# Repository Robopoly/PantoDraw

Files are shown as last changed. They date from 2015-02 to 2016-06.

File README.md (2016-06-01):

# The PantoDraw
The PantoDraw is a device capable of drawing the portrait of people interacting with it. 

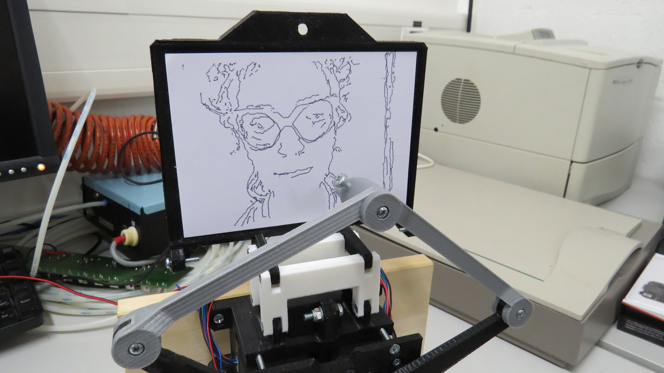
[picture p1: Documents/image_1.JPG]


## Main concept
As visitors always enjoy interacting with robots when visiting Robopoly’s booth at EPFL events, the goal of this project is to give them the opportunity to spend a pleasant time being drawn by a robot-like device. 
By exploiting the capabilities of the [Beagle Bone Black](https://beagleboard.org/black) (BBB), a Texas Instrument single-board powerful computer, and Python programming language, the development team ended up with an original and easy-to-use demonstration of the various skills found at Robopoly.

Operated by a competent user, the device is able to determine the contour of one’s face, compute the optimal path for the pen, and draw the result on a paper the visitor can return with.

An inexpensive webcam and the [OpenCV](http://opencv.org/) image processing library are used for the contours detection. The input image is first converted to grayscale and then goes through a Canny edge detection algorithm, whose parameters can be manually adjusted.
Based on the resulting contours map, a custom algorithm computes the trajectory and minimises the number of branching and raise/drop of the pen.
The resulting image is finally drawn on a paper using three motors: two for the planar movement of the pen and one for the linear movement of the paper support.

## Version 1

The first version of the device was developed for Robopoly’s booth at [Japan Impact](http://www.japan-impact.ch/en/), the annual Japanese convention at EPFL. The process was supervised and control through the Linux terminal using a set of screen, keyboard and mouse connected via a USB hub to the BBB.
The code was rather rudimentary since it was not possible to jump to the previous step, redo the current one or stop the execution. Inverse kinematics equations were computed using a Matlab script, which was also used to optimise the size of the arms.
On the hardware side, servomotors were used, allowing to easily control the pen position with only a few lines of code using the [Adafruit BBB library](https://learn.adafruit.com/setting-up-io-python-library-on-beaglebone-black). Paper was attached to its support by sliding its corners into tiny slits and the complete structure had been 3D printed at Robopoly.

## Version 2

In order to improve the precision - and thus the quality - of the drawing and the usability of the device, both the software and the hardware part have been improved in a second version.
Some servos were replaced by stepper motors, which do not present the internal slack that servos had.
A graphical user interface (GUI) has been designed with Qt Designer and converted to Python using [PyQt4](https://www.riverbankcomputing.com/software/pyqt/intro). It now allows a smooth interaction with the program: it is thus possible to import an image from a file on disk, visualise the different stages of the image, jump to a previous step, change various settings and save them for a future use.
A complete stepper driver module was written with multiple micro-stepping resolutions and a PCB was resigned for the driver integrated chip.

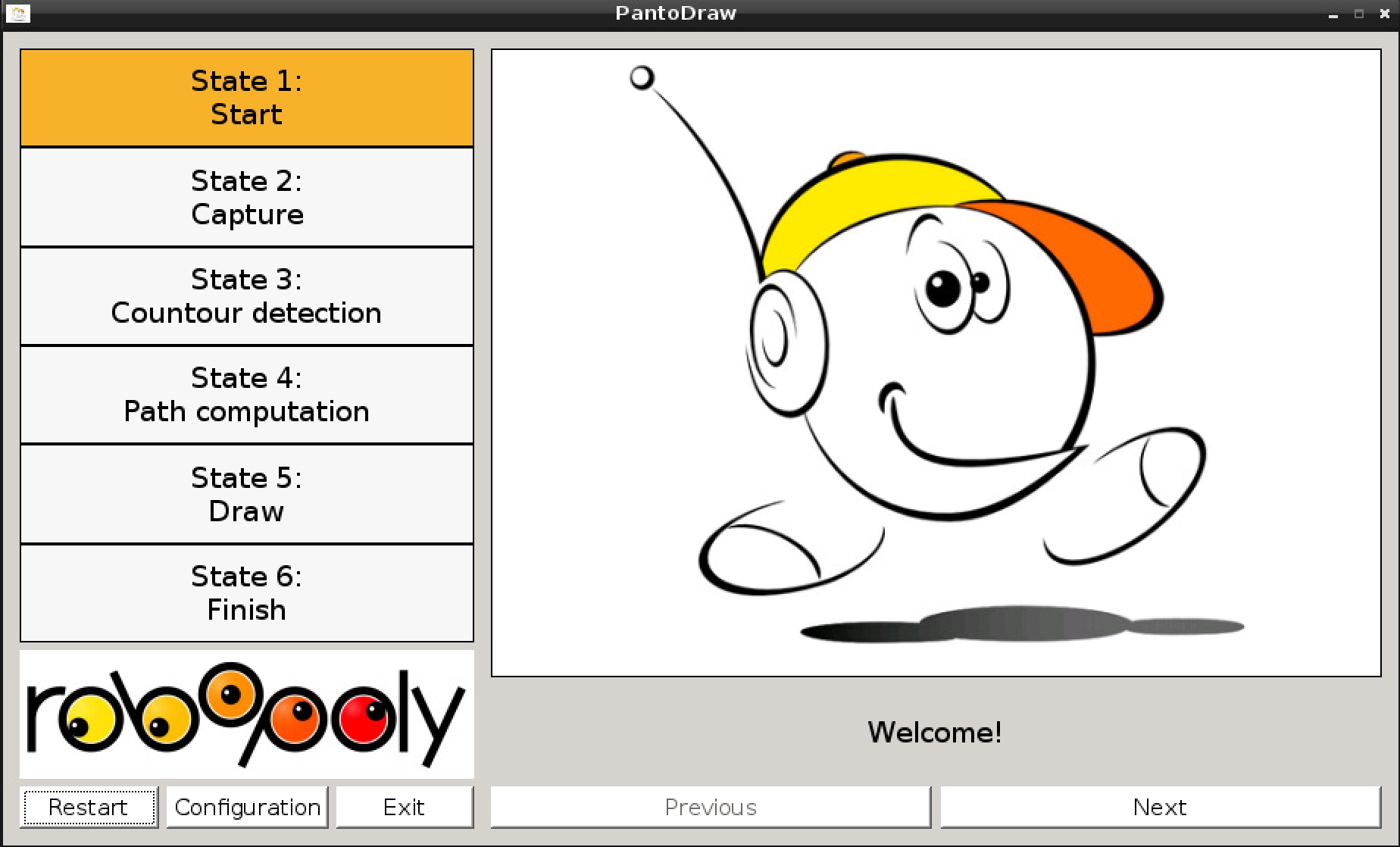
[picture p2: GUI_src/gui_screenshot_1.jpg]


## Hardware

* BeagleBone Black rev. C
* Texas Instrument DRV8823 motor driver
* Bipolar stepper motor 17HM19-2004S (x2)
* Servomotor RS2 MG/BB
* 3D-printed structure
* Folex plotter pen
* A6 paper

## Wiring

The connections to the BBB are:

| Name | Pin |
| ---| --- |
| Driver Data | P9_11  |
| Driver Clock | P9_13  |
| Driver SSTB | P9_15  |
| Driver Chip Select | 5V |
| Servo signal | P9_ 42 |
| VCC | 5V |
| Ground | GND |

The Vbat pin of the driver has to be connected to a DC source which will provide the power for the motors. No exact value is needed since the IC performs a current chop regulation, but there are some conditions: if Vbat is too low, current ramp will be too slow and steps could be missed, but, if V_bat is too high, the driver will dissipate too much heat and its internal thermal shutdown will quickly activate. 20V seems to be working well.

The BBB and the servo have to be powered with a 5V DC source.

The GUI can be accessed with a set of screen/keyboard/mouse or by SSH and VNC with a laptop.

## Use

After boot, the BBB can be access using a simple USB cable connected to a laptop running a VNC client such as Tight VNC Viewer. The address is `192.168.7.2` on port `5900`. The connection requires `X11VNC` to be installed on the board and a simple script to be executed (see folder Documents).

The execution of `main.py` starts the software, including the GUI and the stepper driver module. The user has to make sure both arms are perfectly vertical before launching the drawing.

Future improvement

* Add Endstop micro-switches, allowing to perform an automated calibration of the arms’ position.
* Try a small LCD touchscreen, freeing the operator from the constraint of using a laptop or a screen.
* Improve the pivots could by replacing the 3D printed joints with real bearings.
* Clear the command line script and make it compatible with the modifications introduced by the implementation of the GUI.
* Change the configuration file format from `.py` to `.json` to allow saving of the parameters.

## Credits

Original idea and the first version were developed by Jean-Luc Liardon and Marco Pagnamenta with the help of Pablo Garcia Del Valle, both three members of the Robopoly committee then.

For the second version, the mechanics were designed by Loïs Bosson and Patrick Bobbink, the driver PCB by Yoann Lapijover and the software by Paul-Edouard Sarlin.

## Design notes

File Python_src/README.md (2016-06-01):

# Software

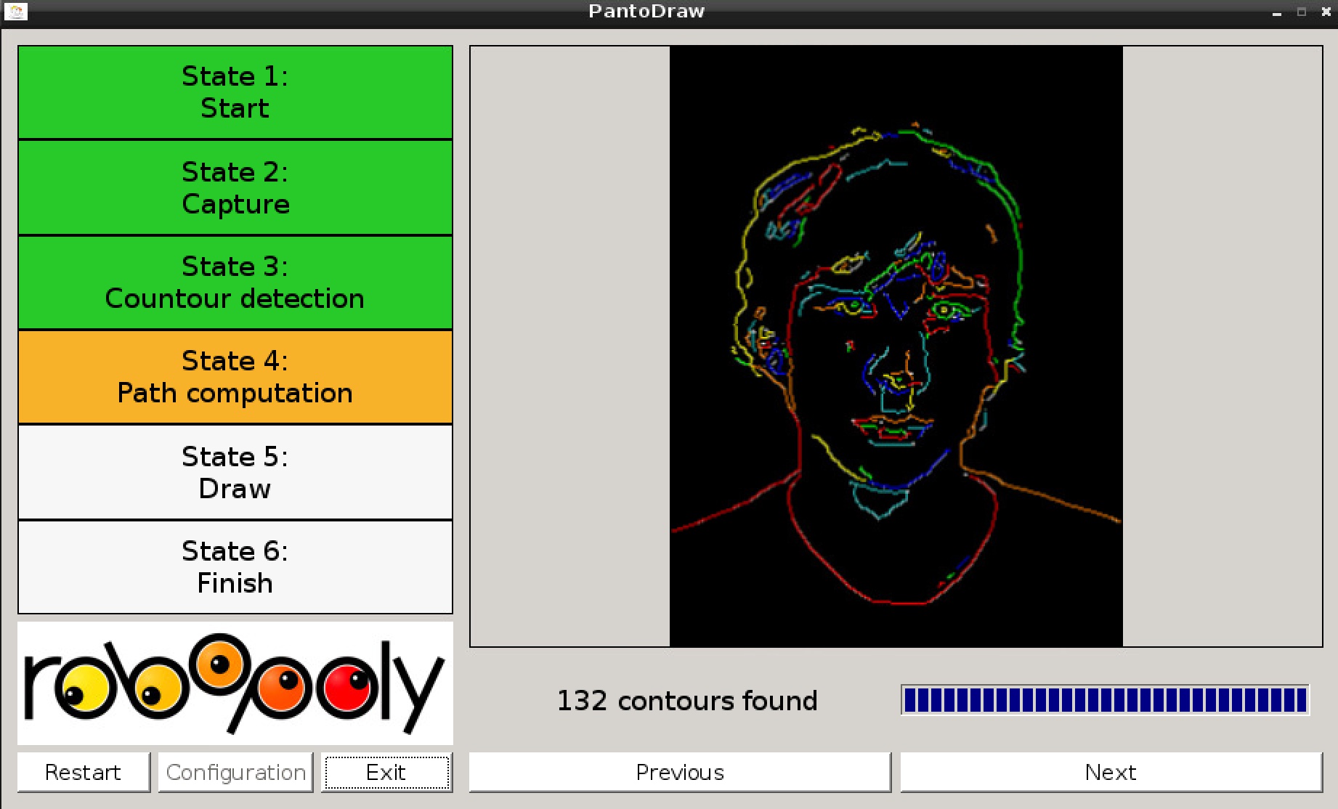
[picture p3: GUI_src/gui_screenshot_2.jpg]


The core application is built around a Finite State Machine (FSM) composed of six states:
* State 1: the starting picture of the software.
* State 2: the acquisition of the image (capture from camera or import from a file on disk).
* State 3: contour detection using the Canny algorithm.
* State 4: path computation and optimisation with display of the different trajectories with various colours.
* State 5: drawing of the result.
* State 6: drawing is finished!

The FSM is directly managed by Qt, running with `main.py`. All the image processing algorithms and OpenCV tools are run in `imageprocessing.py`, which then controls the motor interface (`pantolib_stepper.py` and `stepper.py`).

To ensure that interactions with the GUI are smooth enough even during heavy processing phases, the computations are performed in a separate thread using Python native threading library. The GUI is continuously updated during these phases using `get` functions from the processing module.

Parameters which can be modified by a configuration dialog window in the main application are stored in the `config.py` file and can be easily accessed by the other modules.

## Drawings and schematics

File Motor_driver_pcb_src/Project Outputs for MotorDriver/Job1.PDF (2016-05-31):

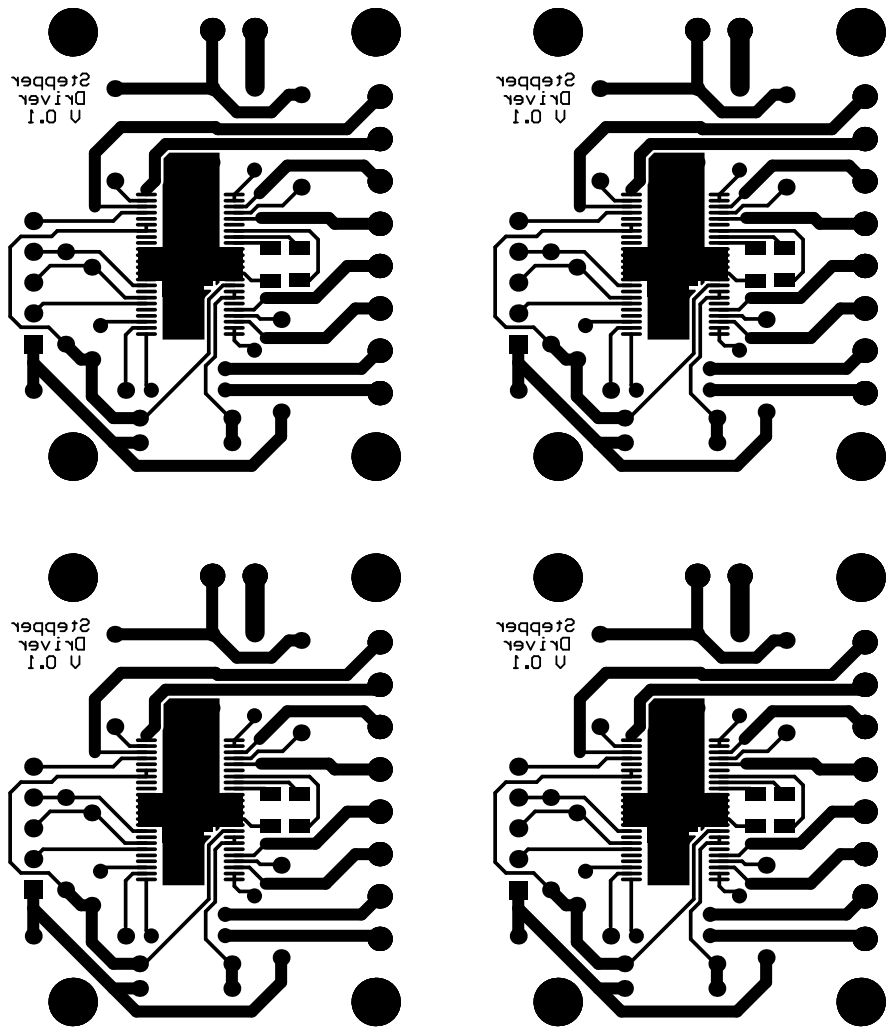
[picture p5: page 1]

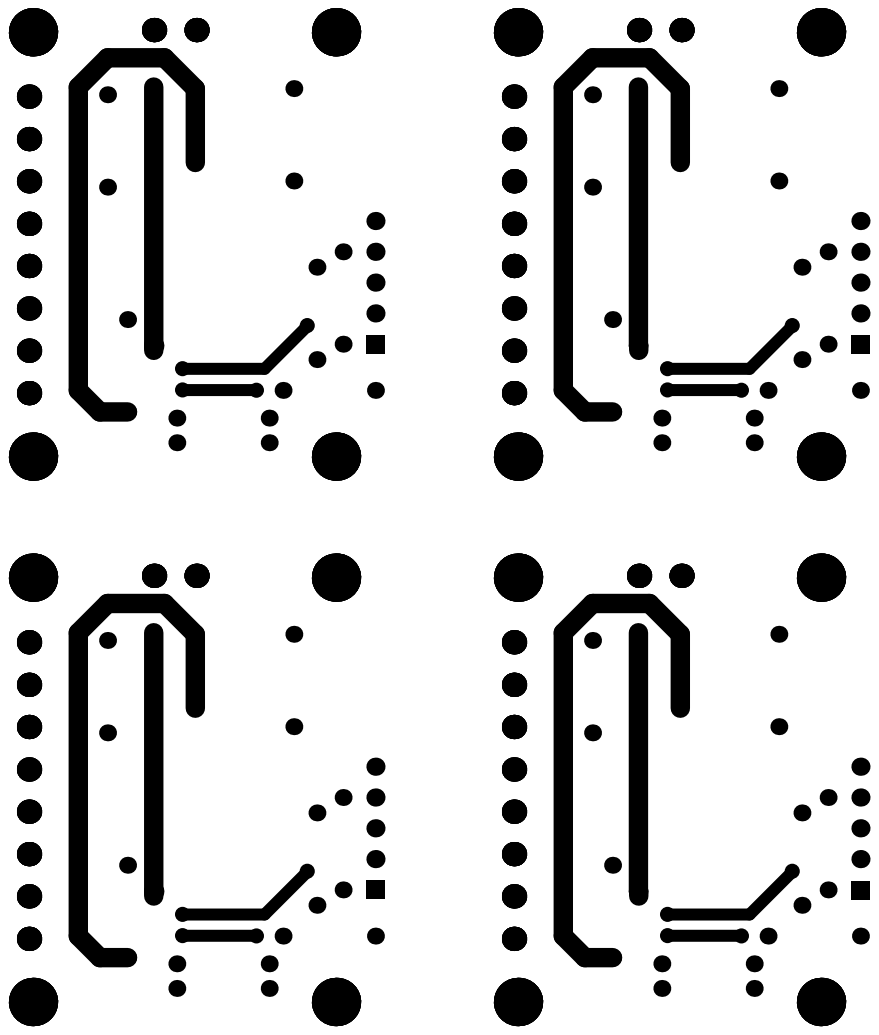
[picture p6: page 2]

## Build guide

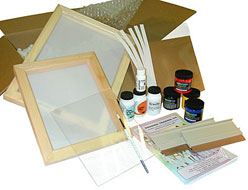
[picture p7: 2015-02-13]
Python_src/Graphical_ressources/printed.jpg

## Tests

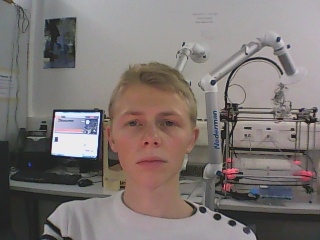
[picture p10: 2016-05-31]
Test_code_src/Contours_detection/test5.jpg

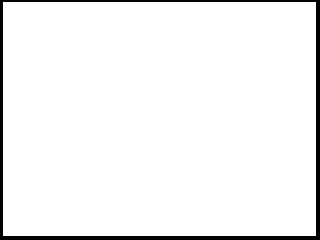
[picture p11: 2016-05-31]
Test_images/Outer_frame.png

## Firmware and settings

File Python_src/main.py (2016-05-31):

###############################################################################
# Copyright (c) 2016, Robopoly Development Team
# All rights reserved.
#
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
# 3. Neither the name of the copyright holder nor the names of its contributors
# may be used to endorse or promote products derived from this software without
# specific prior written permission.
#
# THIS SOFTWARE IS PROVIDED BY THE COPYRIGHT HOLDERS AND CONTRIBUTORS "AS IS"
# AND ANY EXPRESS OR IMPLIED WARRANTIES, INCLUDING, BUT NOT LIMITED TO, THE
# IMPLIED WARRANTIES OF MERCHANTABILITY AND FITNESS FOR A PARTICULAR PURPOSE
# ARE DISCLAIMED. IN NO EVENT SHALL THE COPYRIGHT HOLDER OR CONTRIBUTORS BE
# LIABLE FOR ANY DIRECT, INDIRECT, INCIDENTAL, SPECIAL, EXEMPLARY, OR
# CONSEQUENTIAL DAMAGES (INCLUDING, BUT NOT LIMITED TO, PROCUREMENT OF
# SUBSTITUTE GOODS OR SERVICES; LOSS OF USE, DATA, OR PROFITS; OR BUSINESS
# INTERRUPTION) HOWEVER CAUSED AND ON ANY THEORY OF LIABILITY, WHETHER IN
# CONTRACT, STRICT LIABILITY, OR TORT (INCLUDING NEGLIGENCE OR OTHERWISE)
# ARISING IN ANY WAY OUT OF THE USE OF THIS SOFTWARE, EVEN IF ADVISED OF THE
# POSSIBILITY OF SUCH DAMAGE.
##############################################################################

#######################################################################################
#
# Title:       PantoDraw Project
# File:        main.py
# Date:        2016-05-31
# Author:      Paul-Edouard Sarlin
# Website:	   https://github.com/Robopoly/PantoDraw
#
# Description: Main application managing the GUI and interfacing with the
#              processing module.
#
#######################################################################################


import sys
import cv2
import numpy as np
from PyQt4.QtCore import *
from PyQt4.QtGui import *
import config
from mainwindow import Ui_MainWindow
from configdialog import ConfigDialog
import image_processing as imgproc

GREEN = "background-color: rgb(0,200,0,200)"
ORANGE = "background-color: rgb(255,170,0,200)"
WHITE = "background-color: rgb(255, 255, 255,200)"

# Main application window
class MainApp(QWidget):
	def __init__(self, parent=None):
		super(MainApp, self).__init__(parent)

		self.createUi()
		self.setConnections()
		self.setFSM()

		self.pathTimer = QTimer()
		self.pathTimer.timeout.connect(self.pathCheckThread)

		self.drawTimer = QTimer()
		self.drawTimer.timeout.connect(self.drawCheckThread)
		self.drawing = False

	# Manage graphical details not assessed in the QtDesigner file
	def createUi(self):
		self.ui = Ui_MainWindow()
		self.ui.setupUi(self)
		
		# add graphical ressources used here
		self.logo_robopoly = QPixmap("graphical_ressources/logo_robopoly.png")
		self.pic_bobo = QPixmap("graphical_ressources/bobo.png")

		self.setWindowIcon(QIcon(self.pic_bobo))

		self.ui.Robopoly_logo_label.setScaledContents(False)
		self.ui.Robopoly_logo_label.setPixmap(self.logo_robopoly.scaledToWidth(300,Qt.SmoothTransformation))
		self.ui.image_box.setStyleSheet("")
		self.pic_current = None

		self.ui.canny_thresh1.setValue(2000)
		self.ui.canny_thresh2.setValue(4000)

		# set default window size
		dw = QDesktopWidget()
		self.setFixedSize(dw.width()*0.9,dw.height()*0.7)

	# Manage Signals and Slots
	def setConnections(self):
		self.ui.side_push_exit.clicked.connect(self.exitApp)
		self.ui.side_push_config.clicked.connect(self.configuration)
		self.ui.capture_but.clicked.connect(self.captureImage)
		self.ui.import_but.clicked.connect(self.importImage)
		self.ui.canny_thresh1.sliderMoved.connect(self.displayCanny)
		self.ui.canny_thresh2.sliderMoved.connect(self.displayCanny)
		self.ui.state5_pause_but.clicked.connect(self.pauseDrawing)

	# Manage the FSM parameters
	def setFSM(self):
		self.FSM = QStateMachine()

		self.states = [QState() for i in range(6)] # create a list of 6 states
		self.lastState = 0
		
		# add transition between states with 'Previous', 'Next' and 'Restart' buttons
		for i in self.states:
			self.FSM.addState(i)
			i.setObjectName(str(self.states.index(i)))
		for i in range(0,5):
			self.states[i].addTransition(self.ui.next_but.clicked,self.states[i+1])
		for i in range(1,6):
			self.states[i].addTransition(self.ui.prev_but.clicked,self.states[i-1])
			self.states[i].addTransition(self.ui.side_push_restart.clicked,self.states[0])
		self.states[-1].addTransition(self.ui.next_but.clicked,self.states[0])

		# Set transition Slot
		for i in self.states:
			i.entered.connect(self.enter_state)

		self.FSM.setInitialState(self.states[0])
		self.FSM.start()		

	def reset(self):
		self.ui.canny_thresh1.setValue(2000)
		self.ui.canny_thresh2.setValue(4000)
		self.pic_current = None
		self.pathTimer.stop()
		self.drawTimer.stop()
		imgproc.end()
		imgproc.init()
		self.ui.side_push_config.setEnabled(True)

	# Slot for transition between states
	@pyqtSlot()
	def enter_state(self):
		self.ui.prev_but.setEnabled(True)
		self.ui.next_but.setEnabled(True)
		self.ui.prev_but.setText("Previous")
		self.ui.next_but.setText("Next")

		i = self.states.index(self.FSM.configuration()[0])
		print "State ", i

		if i == 0: # State: Start
			self.reset()

			self.ui.list_state1_label.setStyleSheet(ORANGE)
			self.ui.list_state2_label.setStyleSheet(WHITE)
			self.ui.list_state2_label.setStyleSheet(WHITE)
			self.ui.list_state3_label.setStyleSheet(WHITE)
			self.ui.list_state4_label.setStyleSheet(WHITE)
			self.ui.list_state5_label.setStyleSheet(WHITE)
			self.ui.list_state6_label.setStyleSheet(WHITE)
			self.ui.prev_but.setEnabled(False)
			self.pic_current = self.pic_bobo
			self.dispCurrentPic()

		elif i == 1: # State: Capture
			self.ui.list_state2_label.setStyleSheet(ORANGE)
			if self.lastState == 0:
				self.ui.list_state1_label.setStyleSheet(GREEN)
				self.ui.next_but.setEnabled(False)
				self.ui.image_box.setText("Capture or import a new image")
			else:
				self.ui.list_state3_label.setStyleSheet(WHITE)
				self.pic_current = self.mat2QImage(imgproc.getImage(new=False))
				self.dispCurrentPic()

		elif i == 2: # State: Contour Detection
			self.ui.list_state3_label.setStyleSheet(ORANGE)
			if self.lastState == 1:
				self.ui.list_state2_label.setStyleSheet(GREEN)
			else:
				self.ui.list_state4_label.setStyleSheet(WHITE)
				self.ui.side_push_config.setEnabled(True)

			self.displayCanny(None)

		elif i == 3: # State: Path Computation
			self.ui.list_state4_label.setStyleSheet(ORANGE)
			self.ui.side_push_config.setEnabled(False)
			if self.lastState == 2:
				self.ui.list_state3_label.setStyleSheet(GREEN)
				self.ui.image_box.setText("Computing path... Please wait.")
				self.ui.next_but.setEnabled(False)
				self.ui.prev_but.setEnabled(False)
				imgproc.computePath_launch()
				self.pathTimer.start(0)
			else:
				self.ui.list_state5_label.setStyleSheet(WHITE)
				self.pathCheckThread()

		elif i == 4: # State: Draw
			self.ui.list_state5_label.setStyleSheet(ORANGE)
			self.ui.side_push_config.setEnabled(False)
			if self.lastState == 3:
				self.ui.list_state4_label.setStyleSheet(GREEN)
			else:
				self.ui.list_state6_label.setStyleSheet(WHITE)
				temp, nb_countours = imgproc.computePath_result()
				self.pic_current = self.mat2QImage(temp)
				self.dispCurrentPic()
			self.ui.state5_pause_but.setText("Pause drawing")
			self.ui.prev_but.setEnabled(False)
			self.ui.next_but.setEnabled(False)
			imgproc.draw_launch()
			self.drawing = True
			self.drawTimer.start(0)

		else: # State: Finish
			self.ui.side_push_config.setEnabled(True)
			self.ui.next_but.setText("New drawing")
			self.ui.prev_but.setText("Draw again")
			self.ui.list_state6_label.setStyleSheet(ORANGE)
			self.ui.list_state5_label.setStyleSheet(GREEN)
			self.pic_current = self.pic_bobo
			self.dispCurrentPic()

		self.ui.stackedWidget.setCurrentIndex(i)
		self.lastState = i
		self.repaint()

	# Capture button
	@pyqtSlot()
	def captureImage(self):
		self.pic_current = self.mat2QImage(imgproc.getImage(new=True, capture=True))
		self.dispCurrentPic()
		self.ui.next_but.setEnabled(True)
	# Import button
	@pyqtSlot()
	def importImage(self):
		fileName = QFileDialog.getOpenFileName(self, "Import image", "", "Images (*.png *.xpm *.jpg)")
		if not fileName.isEmpty():
			self.pic_current = self.mat2QImage(imgproc.getImage(new=True, capture=False, path=fileName.toAscii().data()))
			self.dispCurrentPic()
			self.ui.next_but.setEnabled(True)
	# Canny sliders moved
	@pyqtSlot(int)
	def displayCanny(self, thresh):
		self.pic_current = self.mat2QImage(imgproc.computeCanny(self.ui.canny_thresh1.value(), self.ui.canny_thresh2.value()))
		self.dispCurrentPic()		
	# Pause button during drawing
	@pyqtSlot()
	def pauseDrawing(self):
		if self.drawing:
			self.ui.state5_pause_but.setText("Resume drawing")
			self.ui.prev_but.setEnabled(True)
			self.drawing = False
		else:
			self.ui.state5_pause_but.setText("Pause drawing")
			self.ui.prev_but.setEnabled(False)
			self.drawing = True
		imgproc.draw_pause(not self.drawing)
		self.repaint()

	# Check progression during Path Computation
	@pyqtSlot()
	def pathCheckThread(self):
		if not imgproc.computePath_hasFinished():
			progress = imgproc.computePath_progress()
			self.ui.state4_progress.setValue(progress)
			self.ui.state4_label.setText('<html><head/><body><p><span style=" font-size:14pt;">Progress: {0}%</span></p></body></html>'.format(progress))
			self.ui.side_push_restart.setEnabled(False)
		else:
			temp, nb_contours = imgproc.computePath_result()
			self.pic_current = self.mat2QImage(temp)
			self.dispCurrentPic()
			self.ui.state4_progress.setValue(100)
			self.ui.state4_label.setText('<html><head/><body><p><span style=" font-size:14pt;">{0} contours found</span></p></body></html>'.format(nb_contours))
			self.ui.next_but.setEnabled(True)
			self.ui.prev_but.setEnabled(True)
			self.ui.side_push_restart.setEnabled(True)
			self.pathTimer.stop()

	# Check progression during Drawing
	@pyqtSlot()
	def drawCheckThread(self):
		if imgproc.draw_hasFinished():
			self.ui.next_but.setEnabled(True) # manually move to next state
			self.ui.next_but.click()
			self.drawTimer.stop()

	# Start configuration window and gather the new parameters
	@pyqtSlot()
	def configuration(self):
		dialog = ConfigDialog()
		dialog.setWindowModality(False)

		dialog.ui.time_points_value.setValue(config.TIME_BETWEEN_POINTS)
		dialog.ui.time_contours_value.setValue(config.TIME_BETWEEN_CONTOURS)
		dialog.ui.x_offset_value.setValue(config.X_OFFSET)
		dialog.ui.y_offset_value.setValue(config.Y_OFFSET)
		dialog.ui.max_width_value.setValue(config.MAX_WIDTH)
		dialog.ui.max_height_value.setValue(config.MAX_HEIGHT)
		dialog.ui.cam_width_value.setValue(config.CAM_WIDTH)
		dialog.ui.cam_height_value.setValue(config.CAM_HEIGHT)
		dialog.ui.up_angle_value.setValue(config.UP_TABLE)
		dialog.ui.down_angle_value.setValue(config.DOWN_TABLE)
		dialog.ui.home_angle_value.setValue(config.HOME_ANGLE)
		dialog.ui.resolution_value.setValue(config.RESOLUTION)
		dialog.ui.time_steps_value.setValue(config.WAIT_STEP)
		
		if dialog.exec_():
			print "New configuration accepted"

			config.TIME_BETWEEN_POINTS = dialog.ui.time_points_value.value()
			config.TIME_BETWEEN_CONTOURS = dialog.ui.time_contours_value.value()
			config.X_OFFSET = dialog.ui.x_offset_value.value()
			config.Y_OFFSET = dialog.ui.y_offset_value.value()
			config.MAX_WIDTH = dialog.ui.max_width_value.value()
			config.MAX_HEIGHT = dialog.ui.max_height_value.value()
			config.CAM_WIDTH = dialog.ui.cam_width_value.value()
			config.CAM_HEIGHT = dialog.ui.cam_height_value.value()
			config.UP_TABLE = dialog.ui.up_angle_value.value()
			config.DOWN_TABLE = dialog.ui.down_angle_value.value()
			config.HOME_ANGLE = dialog.ui.home_angle_value.value()
			config.RESOLUTION = dialog.ui.resolution_value.value()
			print "New config: ", config.UP_TABLE

	@pyqtSlot()
	def exitApp(self):
		imgproc.end()
		qApp.quit()

	# Utility function for converting OpenCV images (Mat) into Qt ones (QImage)
	def mat2QImage(self,temp):
		temp = cv2.cvtColor(temp, cv2.COLOR_BGR2RGB)
		img = QImage(temp.data, temp.shape[1], temp.shape[0], QImage.Format_RGB888)
		img.bits()
		return QPixmap.fromImage(img)
	# Handle aspect ratio concerns when displaying an image stored in self.pic_current
	def dispCurrentPic(self):
			pic_ratio = self.pic_current.height()/self.pic_current.width()
			size = self.ui.image_box.size()
			label_ratio = size.height()/size.width()
			
			if pic_ratio > label_ratio:
				self.ui.image_box.setPixmap(self.pic_current.scaledToHeight(size.height(),Qt.SmoothTransformation))
			else:
				self.ui.image_box.setPixmap(self.pic_current.scaledToWidth(size.width(),Qt.SmoothTransformation))
			
if __name__ == '__main__':
	qApp = QApplication(sys.argv)
	mainApp = MainApp()
	mainApp.show()
	sys.exit(qApp.exec_())

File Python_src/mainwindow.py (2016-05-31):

###############################################################################
# Copyright (c) 2016, Robopoly Development Team
# All rights reserved.
#
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
# 3. Neither the name of the copyright holder nor the names of its contributors
# may be used to endorse or promote products derived from this software without
# specific prior written permission.
#
# THIS SOFTWARE IS PROVIDED BY THE COPYRIGHT HOLDERS AND CONTRIBUTORS "AS IS"
# AND ANY EXPRESS OR IMPLIED WARRANTIES, INCLUDING, BUT NOT LIMITED TO, THE
# IMPLIED WARRANTIES OF MERCHANTABILITY AND FITNESS FOR A PARTICULAR PURPOSE
# ARE DISCLAIMED. IN NO EVENT SHALL THE COPYRIGHT HOLDER OR CONTRIBUTORS BE
# LIABLE FOR ANY DIRECT, INDIRECT, INCIDENTAL, SPECIAL, EXEMPLARY, OR
# CONSEQUENTIAL DAMAGES (INCLUDING, BUT NOT LIMITED TO, PROCUREMENT OF
# SUBSTITUTE GOODS OR SERVICES; LOSS OF USE, DATA, OR PROFITS; OR BUSINESS
# INTERRUPTION) HOWEVER CAUSED AND ON ANY THEORY OF LIABILITY, WHETHER IN
# CONTRACT, STRICT LIABILITY, OR TORT (INCLUDING NEGLIGENCE OR OTHERWISE)
# ARISING IN ANY WAY OUT OF THE USE OF THIS SOFTWARE, EVEN IF ADVISED OF THE
# POSSIBILITY OF SUCH DAMAGE.
##############################################################################

#######################################################################################
#
# Title:       PantoDraw Project
# File:        mainwindow.py
# Date:        2016-05-31
# Author:      Paul-Edouard Sarlin
# Website:	   https://github.com/Robopoly/PantoDraw
#
# Description: Graphics for the GUI main window. Generated from file
#              'mainwindow.ui' using PYQt4 UI code generator (v. 4.9.3).
#
#######################################################################################

from PyQt4 import QtCore, QtGui

try:
    _fromUtf8 = QtCore.QString.fromUtf8
except AttributeError:
    _fromUtf8 = lambda s: s

class Ui_MainWindow(object):
    def setupUi(self, MainWindow):
        MainWindow.setObjectName(_fromUtf8("MainWindow"))
        MainWindow.resize(984, 645)
        MainWindow.setWindowTitle(_fromUtf8("PantoDraw"))
        self.horizontalLayout = QtGui.QHBoxLayout(MainWindow)
        self.horizontalLayout.setObjectName(_fromUtf8("horizontalLayout"))
        self.StatesOverview = QtGui.QVBoxLayout()
        self.StatesOverview.setSpacing(0)
        self.StatesOverview.setSizeConstraint(QtGui.QLayout.SetDefaultConstraint)
        self.StatesOverview.setContentsMargins(0, -1, -1, -1)
        self.StatesOverview.setObjectName(_fromUtf8("StatesOverview"))
        self.StatesDisplay = QtGui.QVBoxLayout()
        self.StatesDisplay.setObjectName(_fromUtf8("StatesDisplay"))
        self.list_state1_label = QtGui.QLabel(MainWindow)
        font = QtGui.QFont()
        font.setPointSize(14)
        self.list_state1_label.setFont(font)
        self.list_state1_label.setStyleSheet(_fromUtf8("background-color: rgb(255, 255, 255);"))
        self.list_state1_label.setFrameShape(QtGui.QFrame.Panel)
        self.list_state1_label.setFrameShadow(QtGui.QFrame.Plain)
        self.list_state1_label.setTextFormat(QtCore.Qt.AutoText)
        self.list_state1_label.setAlignment(QtCore.Qt.AlignCenter)
        self.list_state1_label.setMargin(8)
        self.list_state1_label.setObjectName(_fromUtf8("list_state1_label"))
        self.StatesDisplay.addWidget(self.list_state1_label)
        self.list_state2_label = QtGui.QLabel(MainWindow)
        font = QtGui.QFont()
        font.setPointSize(14)
        self.list_state2_label.setFont(font)
        self.list_state2_label.setStyleSheet(_fromUtf8("background-color: rgb(255, 255, 255);"))
        self.list_state2_label.setFrameShape(QtGui.QFrame.Panel)
        self.list_state2_label.setTextFormat(QtCore.Qt.AutoText)
        self.list_state2_label.setAlignment(QtCore.Qt.AlignCenter)
        self.list_state2_label.setMargin(8)
        self.list_state2_label.setObjectName(_fromUtf8("list_state2_label"))
        self.StatesDisplay.addWidget(self.list_state2_label)
        self.list_state3_label = QtGui.QLabel(MainWindow)
        self.list_state3_label.setEnabled(True)
        sizePolicy = QtGui.QSizePolicy(QtGui.QSizePolicy.Preferred, QtGui.QSizePolicy.Preferred)
        sizePolicy.setHorizontalStretch(0)
        sizePolicy.setVerticalStretch(0)
        sizePolicy.setHeightForWidth(self.list_state3_label.sizePolicy().hasHeightForWidth())
        self.list_state3_label.setSizePolicy(sizePolicy)
        font = QtGui.QFont()
        font.setPointSize(14)
        self.list_state3_label.setFont(font)
        self.list_state3_label.setStyleSheet(_fromUtf8("background-color: rgb(255, 255, 255);"))
        self.list_state3_label.setFrameShape(QtGui.QFrame.Panel)
        self.list_state3_label.setTextFormat(QtCore.Qt.AutoText)
        self.list_state3_label.setScaledContents(False)
        self.list_state3_label.setAlignment(QtCore.Qt.AlignCenter)
        self.list_state3_label.setMargin(8)
        self.list_state3_label.setObjectName(_fromUtf8("list_state3_label"))
        self.StatesDisplay.addWidget(self.list_state3_label)
        self.list_state4_label = QtGui.QLabel(MainWindow)
        font = QtGui.QFont()
        font.setPointSize(14)
        self.list_state4_label.setFont(font)
        self.list_state4_label.setStyleSheet(_fromUtf8("background-color: rgb(255, 255, 255);"))
        self.list_state4_label.setFrameShape(QtGui.QFrame.Panel)
        self.list_state4_label.setTextFormat(QtCore.Qt.AutoText)
        self.list_state4_label.setAlignment(QtCore.Qt.AlignCenter)
        self.list_state4_label.setMargin(8)
        self.list_state4_label.setObjectName(_fromUtf8("list_state4_label"))
        self.StatesDisplay.addWidget(self.list_state4_label)
        self.list_state5_label = QtGui.QLabel(MainWindow)
        font = QtGui.QFont()
        font.setPointSize(14)
        self.list_state5_label.setFont(font)
        self.list_state5_label.setStyleSheet(_fromUtf8("background-color: rgb(255, 255, 255);"))
        self.list_state5_label.setFrameShape(QtGui.QFrame.Panel)
        self.list_state5_label.setTextFormat(QtCore.Qt.AutoText)
        self.list_state5_label.setAlignment(QtCore.Qt.AlignCenter)
        self.list_state5_label.setMargin(8)
        self.list_state5_label.setObjectName(_fromUtf8("list_state5_label"))
        self.StatesDisplay.addWidget(self.list_state5_label)
        self.list_state6_label = QtGui.QLabel(MainWindow)
        font = QtGui.QFont()
        font.setPointSize(14)
        self.list_state6_label.setFont(font)
        self.list_state6_label.setStyleSheet(_fromUtf8("background-color: rgb(255, 255, 255);"))
        self.list_state6_label.setFrameShape(QtGui.QFrame.Panel)
        self.list_state6_label.setTextFormat(QtCore.Qt.AutoText)
        self.list_state6_label.setAlignment(QtCore.Qt.AlignCenter)
        self.list_state6_label.setMargin(8)
        self.list_state6_label.setObjectName(_fromUtf8("list_state6_label"))
        self.StatesDisplay.addWidget(self.list_state6_label)
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

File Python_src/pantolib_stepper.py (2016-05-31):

###############################################################################
# Copyright (c) 2016, Robopoly Development Team
# All rights reserved.
#
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
# 3. Neither the name of the copyright holder nor the names of its contributors
# may be used to endorse or promote products derived from this software without
# specific prior written permission.
#
# THIS SOFTWARE IS PROVIDED BY THE COPYRIGHT HOLDERS AND CONTRIBUTORS "AS IS"
# AND ANY EXPRESS OR IMPLIED WARRANTIES, INCLUDING, BUT NOT LIMITED TO, THE
# IMPLIED WARRANTIES OF MERCHANTABILITY AND FITNESS FOR A PARTICULAR PURPOSE
# ARE DISCLAIMED. IN NO EVENT SHALL THE COPYRIGHT HOLDER OR CONTRIBUTORS BE
# LIABLE FOR ANY DIRECT, INDIRECT, INCIDENTAL, SPECIAL, EXEMPLARY, OR
# CONSEQUENTIAL DAMAGES (INCLUDING, BUT NOT LIMITED TO, PROCUREMENT OF
# SUBSTITUTE GOODS OR SERVICES; LOSS OF USE, DATA, OR PROFITS; OR BUSINESS
# INTERRUPTION) HOWEVER CAUSED AND ON ANY THEORY OF LIABILITY, WHETHER IN
# CONTRACT, STRICT LIABILITY, OR TORT (INCLUDING NEGLIGENCE OR OTHERWISE)
# ARISING IN ANY WAY OUT OF THE USE OF THIS SOFTWARE, EVEN IF ADVISED OF THE
# POSSIBILITY OF SUCH DAMAGE.
##############################################################################

#######################################################################################
#
# Title:       PantoDraw Project
# File:        pantolib_stepper.py
# Date:        2016-05-31
# Authors:     Jean-Luc Liardon, Marco Pagnamenta,
#              Pablo Garcia del Valle, Paul-Edouard Sarlin
# Website:     https://github.com/Robopoly/PantoDraw
#
# Description: High-level stepper and servo motors control module.
#
#######################################################################################

import Adafruit_BBIO.PWM as PWM
import Adafruit_BBIO.GPIO as GPIO
from stepper import Stepper
import config
from time import sleep

# servo parameters
a_min = 67.
duty0 = 3.
duty180 = 12.
ratio1 = (duty180-duty0)/180
pwm_f = 50

# define pin numbers
B_1 = "P9_12"
B_2 = "P9_14"
SUPPORT = "P9_42"

# define angles
iddleAngle = 150
endAngle1 = 210
endAngle2 = 192

# instantiate stepper objects
s1 = Stepper(1, config.RESOLUTION)
s2 = Stepper(2, config.RESOLUTION)

def Init():
	PWM.start(SUPPORT, ratio1 *  config.DOWN_TABLE + duty0, pwm_f)
        GPIO.setup(B_1, GPIO.IN)
        GPIO.setup(B_2, GPIO.IN)

# WIP function
def NewLaunchCalib():
	s2.inc() #block stepper 2
	Calibrate(s1, B_1, endAngle1)
	Calibrate(s2, B_2, endAngle2)
	sleep(0.5)

#WIP function
def LaunchCalib():
	s1.set(AngleToStep(config.HOME_ANGLE))
	s2.set(AngleToStep(config.HOME_ANGLE))
	Dec1()
	Dec2()

	#s1.wait()
	#s2.wait()
	#GoTo(startAngle, startAngle)

# WIP function
def Calibrate(s, button, endAngle):
        while GPIO.input(button): # buttons are at Vcc when released
                s.inc()
                sleep(config.WAIT_STEP)
        while not GPIO.input(button):
                s.dec()
                sleep(config.WAIT_STEP)
        s.set(AngleToStep(endAngle))
        while s.get() > AngleToStep(startAngle):
                s.dec()
                sleep(config.WAIT_STEP)

def GoTo(a1,a2):
        q1 = AngleToStep(a1)
        q2 = AngleToStep(a2)
        while (s1.get() != q1) or (s2.get() != q2):
                if s1.get() < q1:
                        s1.inc()
                elif s1.get() > q1:
                        s1.dec()

                if s2.get() < q2:
                        s2.inc()
                elif s2.get() > q2:
                 	s2.dec()

                sleep(config.WAIT_STEP)

def SetHome():
	GoTo(config.HOME_ANGLE, config.HOME_ANGLE)

def Inc1():
	s1.inc()
	sleep(config.WAIT_STEP)
def Inc2():
	s2.inc()
	sleep(config.WAIT_STEP)
def Dec1():
	s1.dec()
	sleep(config.WAIT_STEP)
def Dec2():
	s2.dec()
	sleep(config.WAIT_STEP)

# Bring table up
def Up():
	for i in range(config.DOWN_TABLE, config.UP_TABLE+1):
        	PWM.set_duty_cycle(SUPPORT, ratio1 * i + duty0)
		sleep(0.01)
# Bring table down
def Down():
        PWM.set_duty_cycle(SUPPORT, ratio1 * config.DOWN_TABLE + duty0)

# Set coils current to minimum if possible
def Wait():
	s1.wait()
	s2.wait()
# Set coils current to zero
def End():
        s1.end()
        s2.end()

def AngleToStep(a):
        return int(round(a*config.RESOLUTION/0.9))

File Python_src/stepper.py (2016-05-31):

###############################################################################
# Copyright (c) 2016, Robopoly Development Team
# All rights reserved.
#
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
# 3. Neither the name of the copyright holder nor the names of its contributors
# may be used to endorse or promote products derived from this software without
# specific prior written permission.
#
# THIS SOFTWARE IS PROVIDED BY THE COPYRIGHT HOLDERS AND CONTRIBUTORS "AS IS"
# AND ANY EXPRESS OR IMPLIED WARRANTIES, INCLUDING, BUT NOT LIMITED TO, THE
# IMPLIED WARRANTIES OF MERCHANTABILITY AND FITNESS FOR A PARTICULAR PURPOSE
# ARE DISCLAIMED. IN NO EVENT SHALL THE COPYRIGHT HOLDER OR CONTRIBUTORS BE
# LIABLE FOR ANY DIRECT, INDIRECT, INCIDENTAL, SPECIAL, EXEMPLARY, OR
# CONSEQUENTIAL DAMAGES (INCLUDING, BUT NOT LIMITED TO, PROCUREMENT OF
# SUBSTITUTE GOODS OR SERVICES; LOSS OF USE, DATA, OR PROFITS; OR BUSINESS
# INTERRUPTION) HOWEVER CAUSED AND ON ANY THEORY OF LIABILITY, WHETHER IN
# CONTRACT, STRICT LIABILITY, OR TORT (INCLUDING NEGLIGENCE OR OTHERWISE)
# ARISING IN ANY WAY OUT OF THE USE OF THIS SOFTWARE, EVEN IF ADVISED OF THE
# POSSIBILITY OF SUCH DAMAGE.
##############################################################################

#######################################################################################
#
# Title:       PantoDraw Project
# File:        stepper.py
# Date:        2016-05-31
# Authors:     Paul-Edouard Sarlin
# Website:     https://github.com/Robopoly/PantoDraw
#
# Description: Low-level stepper motors control module with class implementation.
#
#######################################################################################

import Adafruit_BBIO.GPIO as GPIO


AEN = 0
APH = 1
BEN = 6
BPH = 7

A10 = 2
B10 = 8

ADEC = 5
BDEC = 11

ADDR = 12

DATA = "P9_11"
CLCK = "P9_13"
SSTB = "P9_15"

# for 20% / 71% / 98% / 100%
current = [0b001, 0b011, 0b101, 0b111]

class Stepper:
        def __init__(self, id=1, resolution=2):
                self.id = id-1 # can be either 1 or 0
                self.count = -1
                self.offset = 0
                self.res = resolution # e.g 2 for half-steps

                GPIO.setup(DATA, GPIO.OUT)
                GPIO.setup(CLCK, GPIO.OUT)
                GPIO.setup(SSTB, GPIO.OUT)
                GPIO.output(DATA, GPIO.LOW)
                GPIO.output(CLCK, GPIO.LOW)
                GPIO.output(SSTB, GPIO.LOW)

        def sendCommand(self, base):
                for i in range(0,16):
                        data = (base & (1 << i)) >> i
                        if data == 1:
                                out = GPIO.HIGH
                        else:
                                out = GPIO.LOW

                        GPIO.output(DATA, out)
                        GPIO.output(CLCK, GPIO.HIGH)
                        GPIO.output(CLCK, GPIO.LOW)
                        GPIO.output(DATA, GPIO.LOW)

                GPIO.output(SSTB, GPIO.HIGH)
                GPIO.output(SSTB, GPIO.LOW)

	# Current sequence is hardcoded for 1/2, 1/4 and 1/8 microsteps
        def computeSeq(self):
                state = (self.count + self.offset)%(4*self.res)
                base = (self.id << ADDR)
		base |= (1 << ADEC) | (1 << BDEC)
	
                if self.res == 2:
                        if state == 0:
                                base |= (1 << AEN) | (1 << APH)
                                base |= (current[3] << A10)
                        if state == 1:
                                base |= (1 << AEN) | (1 << APH) | (1 << BEN) | (1 << BPH)
                                base |= (current[1] << A10) | (current[1] << B10)
                        if state == 2:
                                base |= (1 << BEN) | (1 << BPH)
                                base |= (current[3] << B10)
                        if state == 3:
                                base |= (1 << AEN) | (1 << BEN) | (1 << BPH)
                                base |= (current[1] << A10) | (current[1] << B10)
                        if state == 4:
                                base |= (1 << AEN)
                                base |= (current[3] << A10)
                        if state == 5:
                                base |= (1 << AEN) | (1 << BEN)
                                base |= (current[1] << A10) | (current[1] << B10)
                        if state == 6:
                                base |= (1 << BEN)
                                base |= (current[3] << B10)
                        if state == 7:
                                base |= (1 << AEN) | (1 << APH) | (1 << BEN)
                                base |= (current[1] << A10) | (current[1] << B10)

                if self.res == 4:
                        if state == 0:
                                base |= (1 << AEN) | (1 << APH)
                                base |= (current[3] << A10)
                        if (state > 0) and (state < 4):
                                base |= (1 << AEN) | (1 << APH) | (1 << BEN) | (1 << BPH)
                                base |= (current[3-state] << A10) | (current[state-1] << B10)
                        if state == 4:
                                base |= (1 << BEN) | (1 << BPH)
                                base |= (current[3] << B10)
                        if (state > 4) and (state < 8):
                                base |= (1 << AEN) | (1 << BEN) | (1 << BPH)
                                base |= (current[state-5] << A10) | (current[7-state] << B10)
                        if state == 8:
                                base |= (1 << AEN)
                                base |= (current[3] << A10)
                        if (state > 8) and (state < 12):
                                base |= (1 << AEN) | (1 << BEN)
                                base |= (current[11-state] << A10) | (current[state-9] << B10)
                        if state == 12:
                                base |= (1 << BEN)
                                base |= (current[3] << B10)
                        if (state > 12) and (state < 16):
                                base |= (1 << AEN) | (1 << APH) | (1 << BEN)
                                base |= (current[state-13] << A10) | (current[15-state] << B10)
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

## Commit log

2015-01-14 Added solidworks files
    [Assem1 - arm1-1.STL, Assem1 - arm2-1.STL, Assem1 - arm3-1.STL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]
2015-01-14 Created new mecha piece
    [tablrpiv2.SLDPRT]
2015-01-14 change dimensions table system
    [tablrpiv.SLDPRT, tablrpiv2.SLDPRT]
2015-01-27 Added pieces and asm
    [base.SLDPRT, base.STL, basev2.SLDPRT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]
2015-01-30 improved functional basis
    [basev2.SLDPRT, basev2.STL, motor.SLDPRT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]
2015-02-03 updated mevcha
    [M4toM3.SLDPRT, M4toM3.STL, basev2.SLDPRT]
2015-02-12 updated mechanics
    [basev2.SLDPRT, basev2.STL, pantoDraw.SLDASM]
2015-02-13 Added define to debug in the PC
    In the PC there is no GPIO library, for instance… replaced by a dummy.
    [config.py, pantolib_dummy.py]
2015-02-14 Works with Logitech C170 camera
2015-02-14 updated pieces
    [tablrpiv.SLDPRT, tablrpiv.STL, tablrpiv2.SLDPRT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]
2016-05-31 Removed deprecated mechanical models
    3D printed models are deprecated for v2 since we changed servos for
    stepper motors.
    [Assem1 - arm1-1.STL, Assem1 - arm2-1.STL, Assem1 - arm3-1.STL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]
2016-05-31 Added design sources for the motor driver PCB
    [Main_v0.1.SchDoc, Mainv0.1.PcbDoc, MotorDriver.PrjPCB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]
2016-05-31 Added a picture of the PCB
2016-05-31 Added intermediate test code (Python and Arduino)
